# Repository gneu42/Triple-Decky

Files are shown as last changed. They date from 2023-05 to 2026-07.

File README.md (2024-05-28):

<h1 align="center"><ins>Triple-Decky Filament Block</ins></h1>

<H2 align="center">Filament block with  triple decks for ERCF V1/V1.1, Sturdy Bunny and ERCF V2.</H1>

## What is it ?

**Triple Decky** is based on the Sturdy Bunny filament block from **Sneakytreesnake** that incorporate the MR85ZZ bearing making the need for bearing blocks obsolete. It is a replacement for the filament block on ERCF V1 and Sturdy Bunny. Its goal is to avoid the filament to move in or out the filament block while loading or unloading another gate.
To do that, the filament block consist in 2 hinged parts (decks), that are kept apart by magnets. The filament is lifted by 1 mm from the bottom BMG gear.
The tophat comes on top of the 2nd deck and has the top BMG gear as before.
An integrated tophat based on number 1 tophat locker to be used with Springy [from Moggieuk](https://github.com/moggieuk/ERCF-Springy/tree/main) on Rev B and C.
Although Rev B version still has the possibility to install the magnetic gate, it is normally not needed anymore.
It will not be possible to install the magnetic gates on Rev C.
The width is 23.05mm as the latest Sturdy Bunny filament block that incorporate the bearing in the block.
To take all the benefit of the Trple Decky Filament Block, it is recommended to use a good buffer system (preferably a single loop buffer) The PTFE tube should not apply down force on the ECAS so the magnet can do their work correctly.
For people who needs a bypass block, there will be one incorporated in the "filament block end" of ERCF V2. A stand alone Bypass block that can be placed anywhere on the 2020 extrusion is also available on the triple decky Github. (Bypass_with_ECAS.STL) 
***
## Summary.
* **[Bom](#bom)**
* **[Printing Tips](#printing-tips)**
* **[Cleaning tips](#cleaning-tips)**
* **[Assembling tips](#assembling-tips)**
* **[Triple Decky for Sturdy Bunny and ERCF V2](#triple-decky-for-sturdy-bunny-build-on-a-2020-extrusion)**
  * **[Revision C for 3 positions servo "3PS"](#triple-decky-for-3-positions-servo-brake-release)**
    * **[Important note about Rev C 3 positions servo](#important-note-about-the-3ps-version)**
  * **[Revision C for magnet release brake ](#triple-decky-for-magnet-brake-release)**
  * **[Revision B ](#triple-decky-rev-b)**
* **[Triple Decky for ERCF 1.1](#triple-decky-for-ercf-v1)**
***
## Latest updates.

* #### Savox Servo arm C9 for original horn <sub>*May 28, 2024*</sub>
  * In my opinion, the weakest point of the ERCF are the servo splines. This servo arm solves that problem by using the original 4 branches horn delivered with the Savox servo. It will also work with trimmed MG90 horn. 
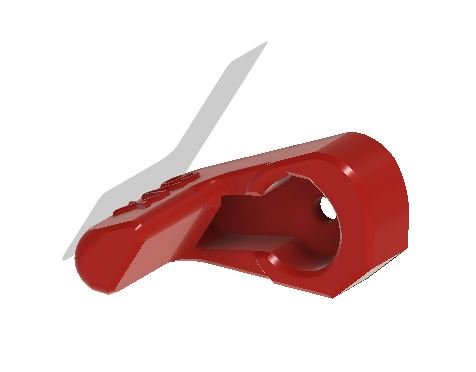
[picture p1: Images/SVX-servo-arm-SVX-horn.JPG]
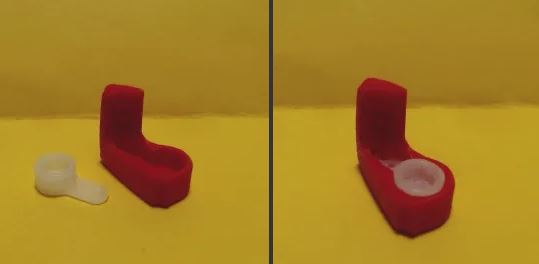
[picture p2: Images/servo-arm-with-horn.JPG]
servo-arm-with-horn
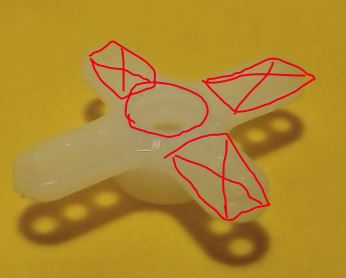
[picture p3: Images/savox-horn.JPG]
   
* #### Triple Decky C9.x <sub>*Apr 27, 2024*</sub>
**<p align=center>If this is your first time printing Triple Decky, it is best to print the C9.x version. However if you have already printed the C7.x parts, and they are freely working together, there is no benefit to upgrade to C9.<br> </p>**
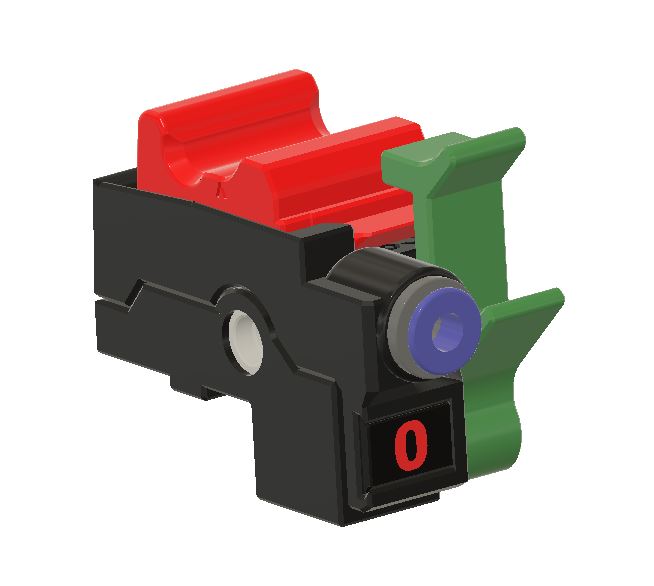
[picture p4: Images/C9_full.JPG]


  * Revision C9.x brings an almost build-in supports free. There is still one build-in support on the tophat.
    * The latch is modified for better integration with Cotton Tail and the new modified base. 
    * The base is shorter and the small latch centering part should not break anymore if the screw is screwed in correctly.
    * The entry tag plate is move from the base the filament path. This makes it easier to install the tag plates after the ERCF unit is build and functioning. The tag plates can then be printed in multi-color with the freshly build unit.
    * The trap design is modified to accommodate the support free base. It is now connected to the base with an M2x10 screw.
    * The tophat has a lower profile than the previous version. This should fix the servo down problem that some users have encountered.
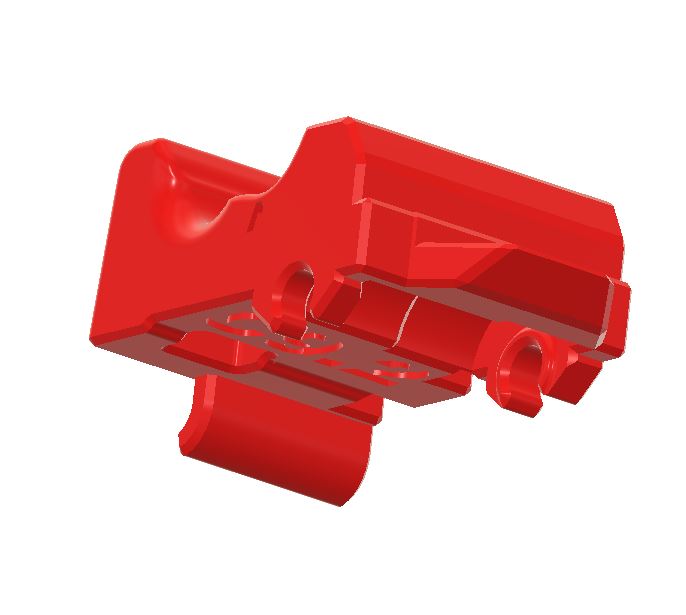
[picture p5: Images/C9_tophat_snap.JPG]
    * There is an optional tophat with sanp-in BMG.
    * There are 2 versions of C9S which incorporate a pre-gate sensor Those versions are made for people with limited space and that does not want to use the Cotton Tail version of the pre-gate sensors.
      * This version of pre-gate sensor is optimized to avoid false triggerinig if the filament have a notch ground from previous bad load.
      * The 5.5mm ball is replaced by a 6x3mm magnet for more stability of the anti-false triggering device.
      * Although this version works very well for automatic insertion of the filament, it may or may not work well for endless spool. 
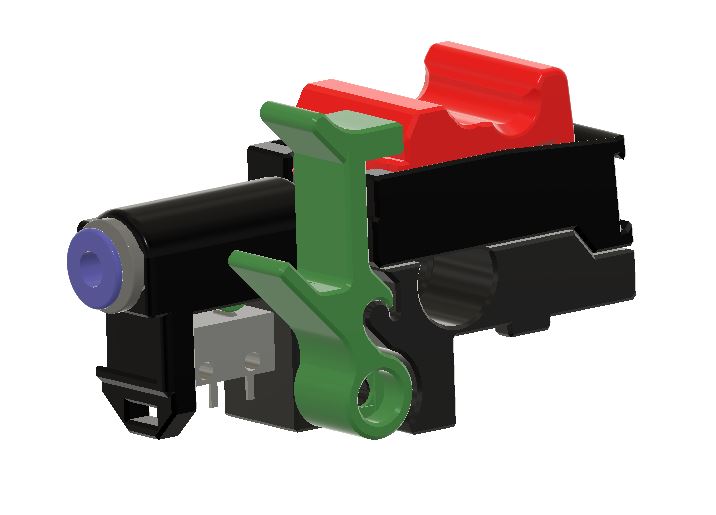
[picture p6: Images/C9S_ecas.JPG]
      * One version uses an ECAS to hold the PTFE tube.
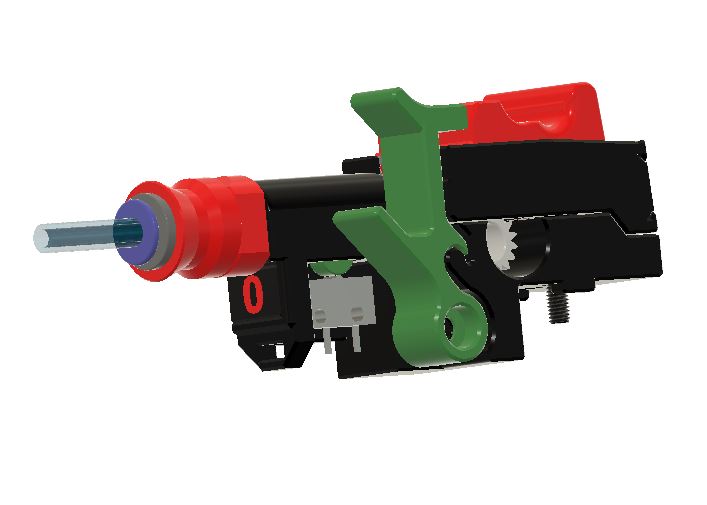
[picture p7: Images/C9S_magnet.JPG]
      * The other uses magnets to hold the PTFE in the filament path.

  * The C9S Pre-gates Sensor STL are in the **Optional Pre-gate Sensor** folder of Rev_C9. See readme file of the folder for more details.
  
  **IMPORTANT NOTE : The C9.x parts are not compatible with the previous C7.x version.**

* #### Triple Decky C7.0 <sub>*Oct 11, 2023*</sub>

  Revision C7.0 brings a few changes to the 3 main parts of Triple Decky. 
  * The big change is on the tophat that gives 2 alternatives. 
    * In one single part with a better support
    * In 2 parts with one support only. The 2 parts are screwed together with M2x10 self tapping screws.
    * This new revision applies only to the 3 positions servo. It will not be compatible with encoder that has the old magnets that were opening the gates on ERCF V1.1
  * The filament path has 2 main changes 
    * It width is reduced by 1 layer (0.2mm) to make sure that they do not rub against each other in case the blocks are installed too tight together.
    * The main support geometry is changed to be easier to print and removed.
    * Two optional clearance versions are available in the clearance option folder. This should make it easier to print with "not too well" tuned printers.
      * the female hinge of Clearance1 is 0.1mm wider than the default part.
      * the female hinge of Clearance2 is 0.2mm wider than the default part.
  * The base has no significant changes beside the 2 clearance options. Also available in the clearance options folder.
  * Tag plates are now available up to 15 gates.

  ##### Tophats C7.0   

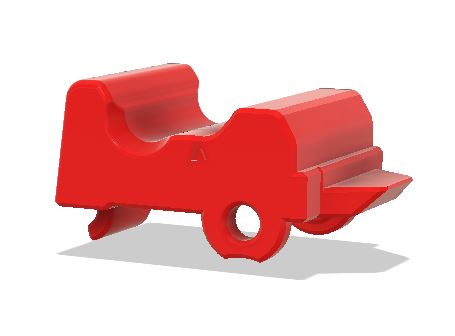
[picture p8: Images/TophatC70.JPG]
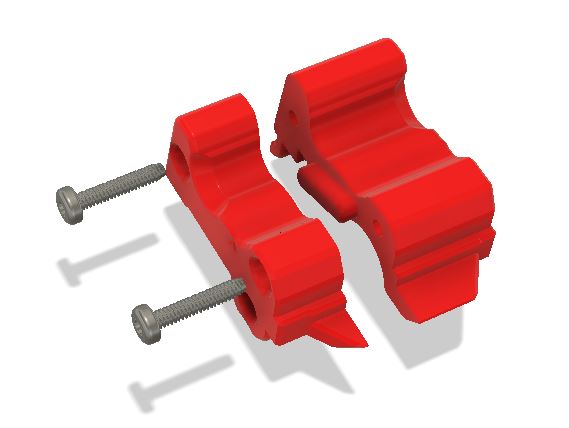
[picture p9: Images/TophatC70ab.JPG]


On the clearance option parts, there are 1 or 2 dots beside the code "C7.0" for the 0.1mm and 0.2mm wider cavities.

  ##### Filament Path C7.0
  
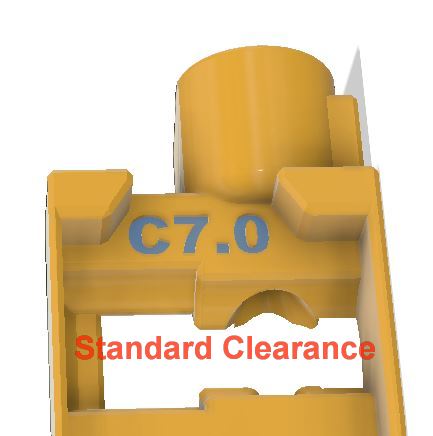
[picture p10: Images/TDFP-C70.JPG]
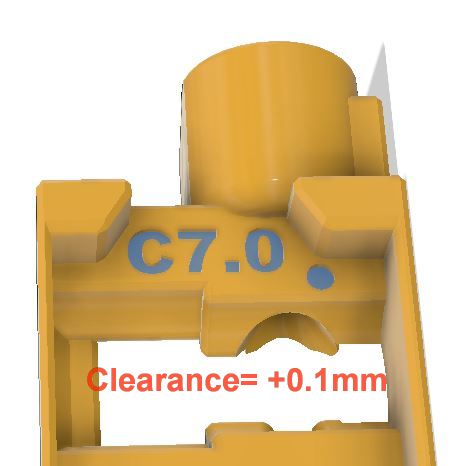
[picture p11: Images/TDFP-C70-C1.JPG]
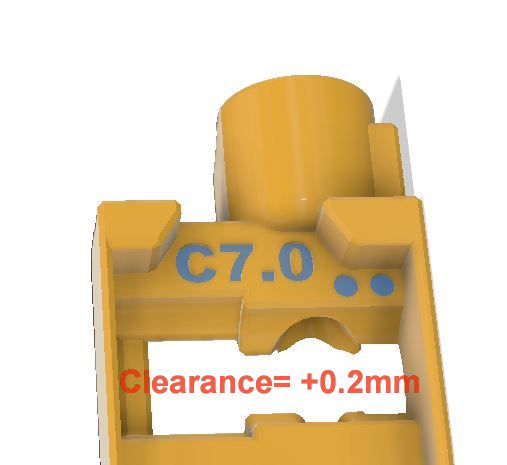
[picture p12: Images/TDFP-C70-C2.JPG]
<p align=center>  
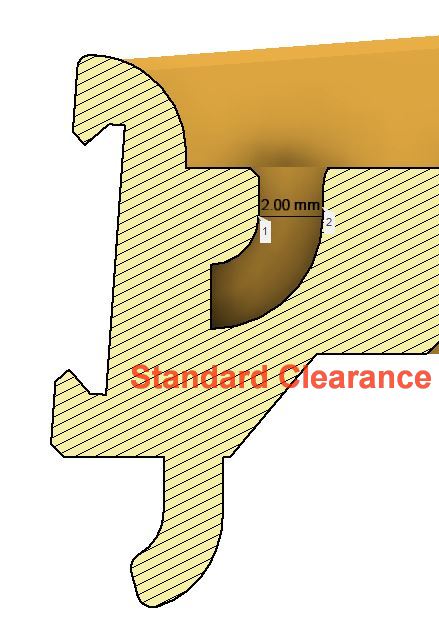
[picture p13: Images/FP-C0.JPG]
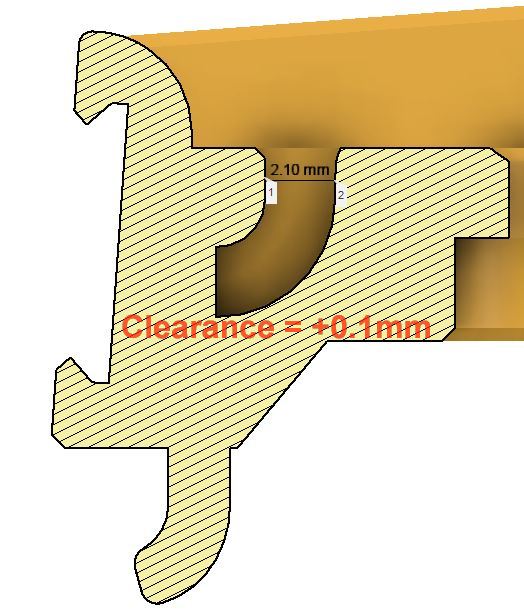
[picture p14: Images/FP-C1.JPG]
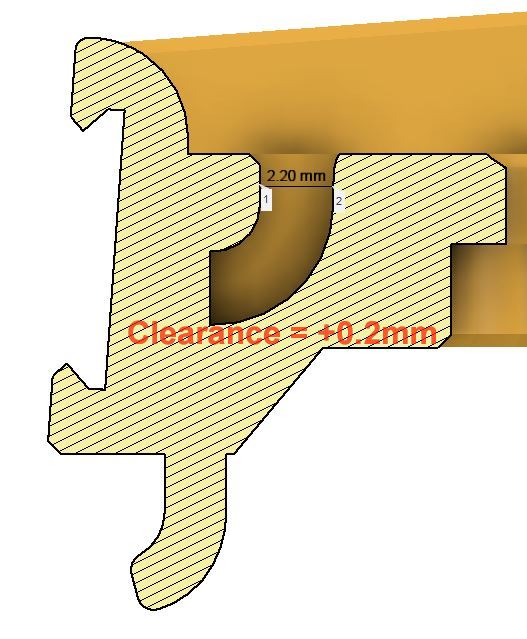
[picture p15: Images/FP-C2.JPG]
<p align=center>  

  ##### Base C7.0

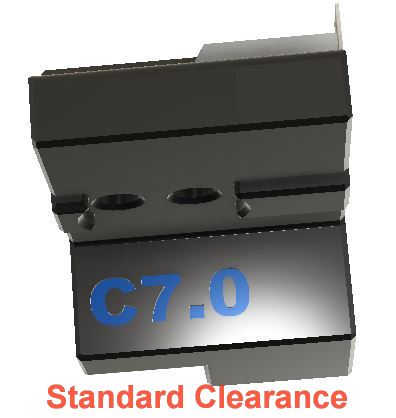
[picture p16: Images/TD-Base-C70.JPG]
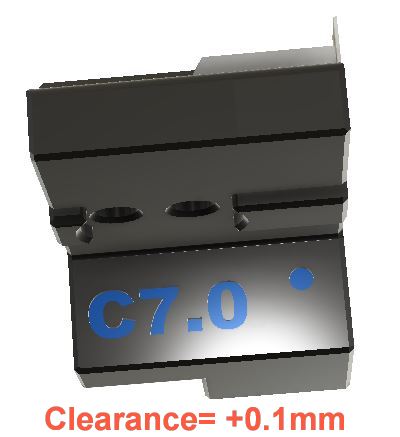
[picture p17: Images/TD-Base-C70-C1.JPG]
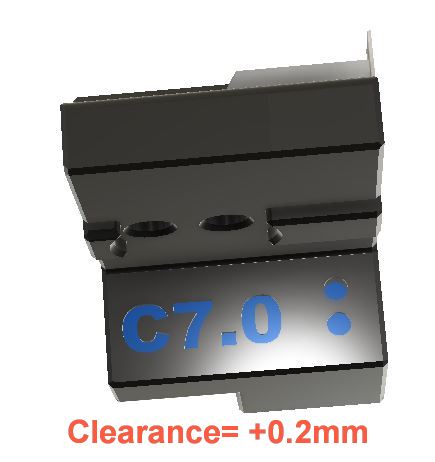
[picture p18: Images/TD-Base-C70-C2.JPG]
<p align=center>  

* #### Triple Decky Base C6.3. <sub>*Aug 31, 2023*</sub>
  
  No change in the main geometries. Only aesthetic change to blend better with filament path C6.3.

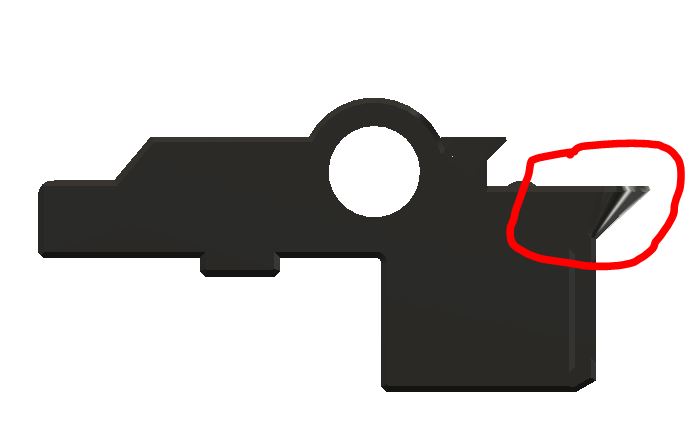
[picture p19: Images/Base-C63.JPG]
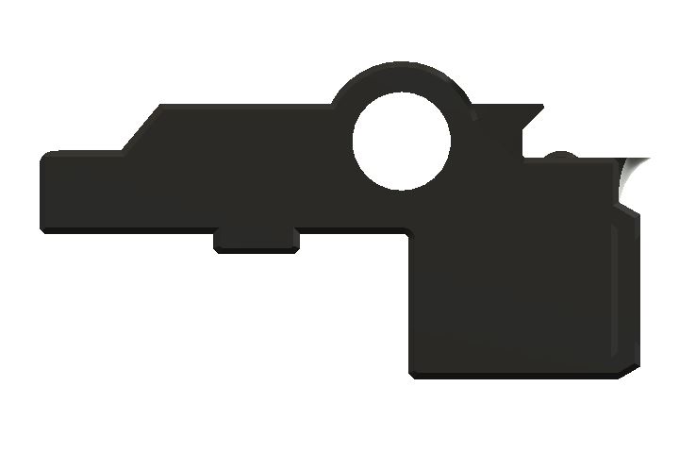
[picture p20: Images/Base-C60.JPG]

<p align=right><sub>You can still find the Triple_Decky_Base_C6_0.stl in the archive folder.</sub>

* #### Stand alone Bypass Block with ECAS. <sub>*Aug 25, 2023*</sub> 
     
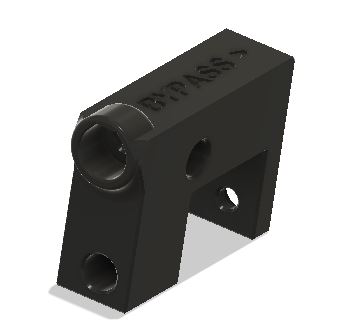
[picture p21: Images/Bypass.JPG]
   <p align=center>You can find it in stl/sturdy bunny</p>
  
* #### New Filament Path Rev C6_3. Read more about it [here](#update-6_3). <sub>*Aug 25, 2023*</sub> 

* #### Triple Decky Rev C for 3 positions servo STLs. Make sure to read the [Important Note Below](#important-note-about-the-3ps-version) first !!!

* #### Triple Decky Rev. C. Read the details [here](#triple-decky-rev-c)

***
## **Yet in development :**
* **ERCF V2 :** at this moment, ERCF V2 is in development by a team of designers. Lots of things have been developed and are tested, but regarding the filament blocks, no decision have been taken on which version of Triple Decky or another type will be used.
  * Mods in progress :
    * Sturdy Bunny: https://github.com/sneakytreesnake/SturdyBunnyProject
    * Springy: https://github.com/moggieuk/ERCF-Springy/tree/main
    * Ejection Assisted Purge: https://github.com/bombela/EjectionAssistedPurge
    * Binky: https://github.com/mneuhaus/EnragedRabbitProject/tree/main/usermods/Binky

**I have re-structured this GitHub to show only the latest versions of each type. All previous STLs are available in the Archives folder.**
***
## BOM.
For each block you need :  
  * #### Rev B.
    * 1 M3x8 SHSC (to mount the base on the 2020 extrusion)
    * 1 M3x16 SHSC (to mount the latch on the base)
    * 2 6x3 magnets (between the base and the filament path)
    * 1 ECAS (on the filament path)
    * 1 set of BMG (on the D-shaft in the base and in the top hat)
  * #### Rev C magnet release trap.
    * 1 M3x8 SHSC (to mount the base on the 2020 extrusion)
    * 1 M3x16 SHSC (to mount the latch on the base)
    * 1 M3x3 set screw. Length: from 2 to 3mm (to install in the trap) (M3x2 can be found in BMG).
    * 3 6x3 magnets (between the base and the filament path and at the back of the filament path)
    * 1 ECAS (on the filament path)
    * 1 set of BMG (on the D-shaft in the base and in the top hat)
  * #### Rev C 3 positions servo release trap.
    * 1 M3x8 SHSC (to mount the base on the 2020 extrusion)
    * 1 M3x16 SHSC (to mount the latch on the base)
    * 1 M3x3 set screw. Length: from 2 to 3mm (to install in the trap) (M3x2 can be found in BMG).
    * 2 6x3 magnets (between the base and the filament path)
    * 1 ECAS (on the filament path)
    * 1 set of BMG (on the D-shaft in the base and in the top hat)
    * Optional : 2 M2x10 self tapping screws for the 2 parts tophat.<p>
   
   <font size="2">[Summary](#summary)
*** 
## **Printing tips:**
  * Make sure your **printer is well tuned**, especially the first layer height. If it is too thick, the brake (trap) will be too thick and will not move freely inside the filament path.
  * All STL were tested OK with ABS and ABS+ 
  * Use voron standard print profile ( I use Andew Ellis ABS print profile).
  * **The hinged parts are the trickiest.** Make a test with one set of parts to see if they fit together freely. Some users have reported that decreasing the "extrusion multiplier" by a few %, makes the parts go together much better. 
  * The 3 main parts are fitting together using a kind of hinge. They should fit together without filing and with a little bit of play. 
  * For unknown reason, Super Slicer and Prusa slicer reports 6 open edges on the filament path STL. **DO NOT try to fix it**, otherwise you will have support that are filled up with infill and more than one perimeter thick. 
  * Make sure you have "Thin wall" enable, otherwise you won't have supports. Set also the speed for thin wall around 50% of the external perimeter speed.
  * It is also better to print a few spare traps. The sides are quiet thin, and it could be possible to break one if you remove the filament path too often.
  * If you plan to print the tag plates in multicolor :
    * You already have a working ERCF, then no problem, just print them before assembling ERCF V2
    * This is your first ERCF build. Then you have 2 possibilities.
      * You can print them multicolor the old way, by changing color manually. The change of color is only 4 layers high, so it is not so difficult.
      * You can print them after you have your new ERCF V2 working, and install them.
        * On the base, you will have to shift each of the bases to allow the insertion of the tag plate
        * On the Filament Path, just remove it, insert the tag plate and re-install the Filament Path. <p>
  
   <font size="2">[Summary](#summary)
***
## **Cleaning tips:**
  * All support should come off very easily.
  * There should be very little part cleaning necessary
    * Using a 2mm drill bit, clean the filament path
    * using a needle file, clean the rectangular hole where the trap is going in on the filament path
    * The trap part should have a thickness of 3.05mm, use a file to make it <= 3.05mm or tune your first layer.
    *  Make sure that the rectangular hole in the filament path Rev C is clean so the trap/brake can fit loosely in. There should be 0.5mm clearance.
    * On the screw trap part you need to make sure that there are no plastic between the thread of the set screw and the filament. Use a sharp x-acto knive to open the space between the 2 holes.
   
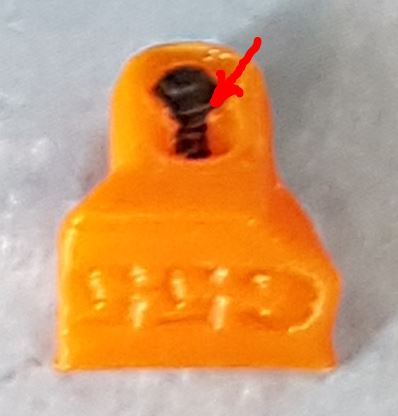
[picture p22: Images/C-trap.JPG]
    
    
    * On Rev C with magnet brake release, make sure the hole for the back magnet is clean, the magnet should go down against the bottom of the hole.  
    * On the tophat up to version C6.2 it could be possible that depending on the type of ABS(+) you're using, the tophat does not move as freely as needed. To solve that, you can cut or file down one layer off from the tang on the support side. This is fixed in the next version C6.3. I only encounter that problem with my ESUN Green ABS+.

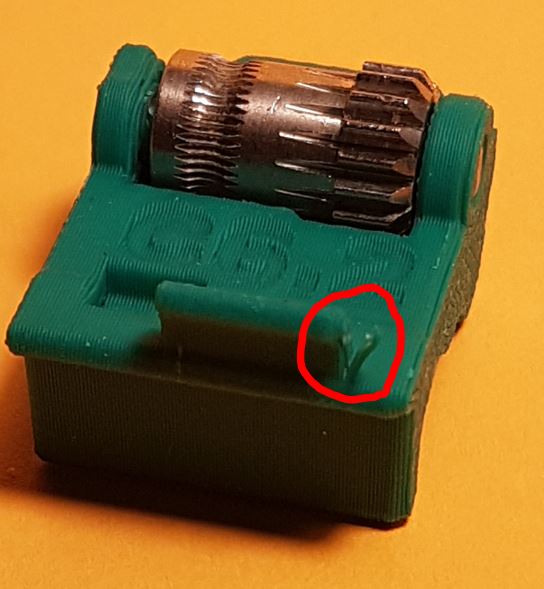
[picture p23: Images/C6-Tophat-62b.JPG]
    
      
       <font size="2">[Summary](#summary)
***
## **Assembling tips:**
**For all Triple Decky versions, when installing the blocks on the 2020 extrusion, it is not necessary to press the blocks firmly together. Just install them on the 2020 extrusion next to each other and tighten the screw. If you press them too much together, it is possible the filament pass does not move freely between their neighbors. This problem is solved in Revision C7.0**
  * Rev B is self explanatory. The 3 parts goes together by sliding the tangs into the correponding cavities that makes the hinges.
  * Rev C need a bit more attention to assemble the filament path on the base.
    * 1. Insert the M3x8 SHCS screw into the side hole of the base before installing the filament path. You will be able to access the screw through the filament pass later. (If you want to use 4 magnets, than you need to install the base on the 2020 extrusion before installing the magnets and filament path. 4 magnets are normally not necessary.)

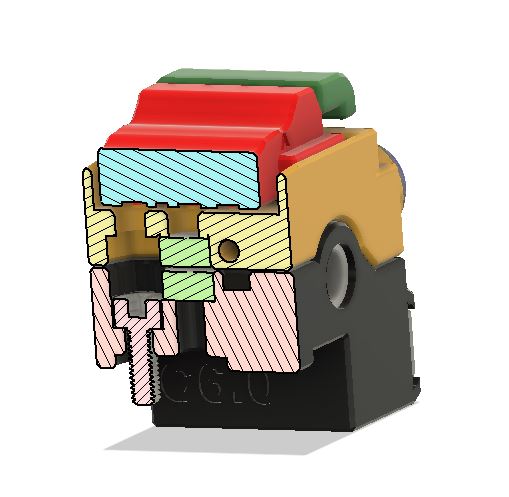
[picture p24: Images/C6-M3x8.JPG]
      

    * 2. Insert the magnet into the middle holes of the base and the filament path. The magnet must repell each other.
      * Optionally, you can use another set of magnet into the side holes if needed. In that case, the screw will be unaccessible without disassembling the parts
    * 3. Insert the trap into the female dovetail.
      * If you use the screw trap, insert the set screw at a slight angle. The 2 holes are angled by about 2°. Insert the set screw in the top hole. <BR>
      The set screw can be :
        * M3x3mm
        * M3x2.5mm
        * M3x2mm, the same that you can find in the BMG.   
       
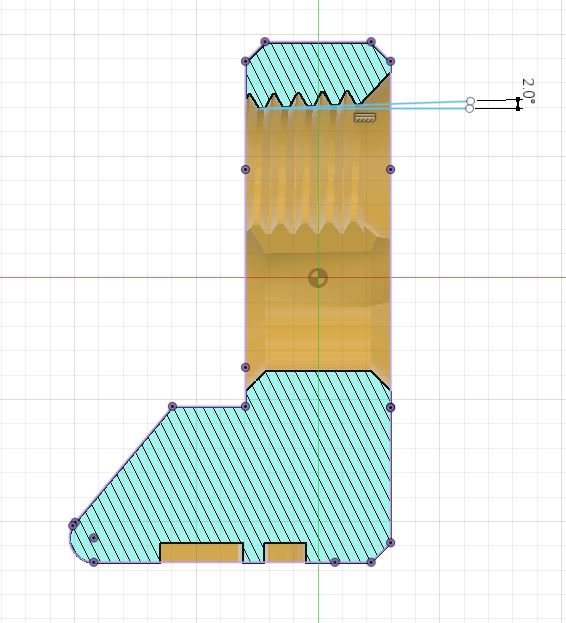
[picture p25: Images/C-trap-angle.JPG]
      

    * 4. Align the filament path above the base so they are parrallel and the top of the brake (trap) is "almost" inside his corresponding hole in the filament path and the tang of the hinge is just above the cavity of the base. 
     
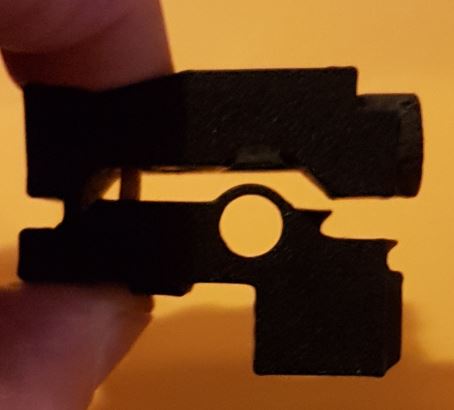
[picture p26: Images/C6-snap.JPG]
      
    
    * 5. Press firmly the filament path into the base. It snap into place easily.
    
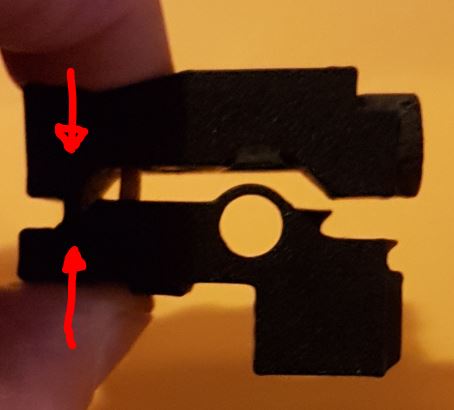
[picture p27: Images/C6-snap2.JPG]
      

  * Magnets orientation.
  
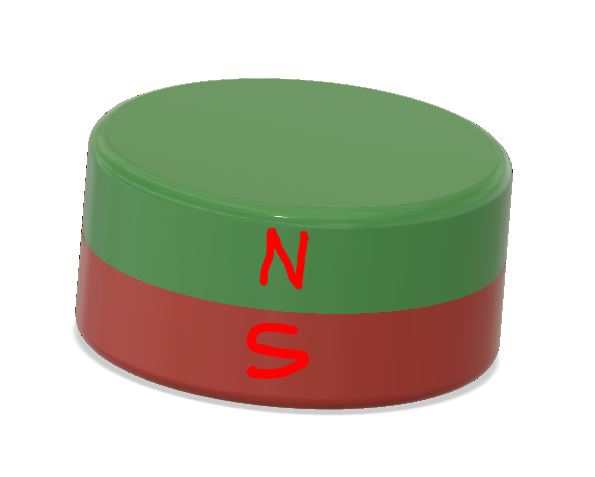
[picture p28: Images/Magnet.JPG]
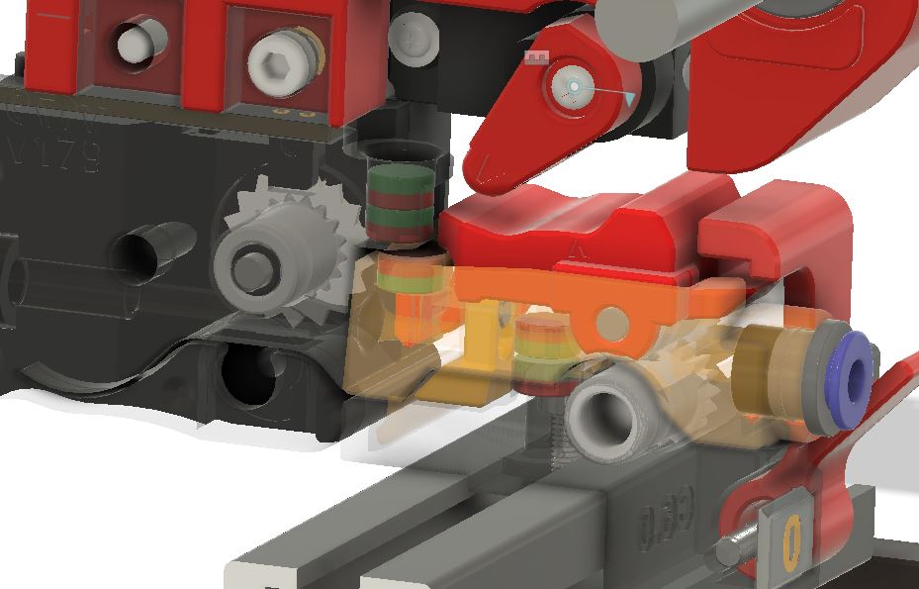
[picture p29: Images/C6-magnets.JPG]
       

  * Assembling video.<br>
  This video shows how parts fits together out of the printer without any filing nor sanding. Then how Triple Decky works with one pair of magnets and the movement you should have at the back and front side. And finally how to install the trap.
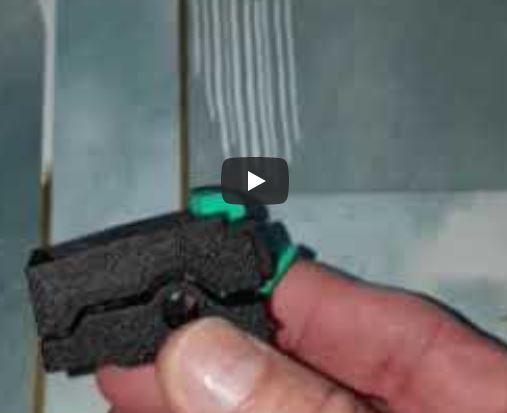
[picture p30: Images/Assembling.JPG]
Assembling
   <p align=center>  

<font size="2">[Summary](#summary)

***
## Triple Decky for Sturdy Bunny build on a 2020 extrusion 
 ### Triple Decky Rev C
   **It is an evolution of Rev B. with the following new features.**
   *  It has a kind of brake to press against the filament when the gate is not selected. The exit side of the filament path can lift up about 0.5 mm, enough to make the filament touching the brake part (trap). To release the brake it will use either :
        *  with a magnet that will be pushed back by the encoder magnet.
        *  by using a special tophat that will need a 3rd position of the servo to be able to move the selector. (software in development)<p>
   * The brake part will be easily replaceable in case it breaks.
   *  The multi-color tag plates will be the same for input and output side. (Same as in version B4 Base)<p>
   *  The use of the old magnetic gates will be **impossible** on that version.
   *  If you are using Happy Hare software, you should decrease the "parking_distance" in the ercf_parameters to about 15 so the filament parks inside the trap.
   *  It is normal that the filament does not pass the trap when inserted manually. When the gate will be selected, Happy Hare will load it without problem. If you want to lock it inside the trap, than you need to push down the exit side of the filament path with your finger and insert the filament about 5 mm further.<p>

<font size="2">[Summary](#summary)
***  
### **Triple Decky Rev C6 magnet brake release or 3 positions servo.** 

#### Update 6_3 
 This update concern all **Filament Path revision B and C for Sturdy Bunny**. The ECAS is moved 4mm out to enable the insertion of the PTFE tube inside the part. I recommend to use it over the previous versions.
 * This allow for easy threading of the filament and keeps also the geometry for Endless Spool function.
 * It avoids the ECAS to go slowly out of its cavity after some time.

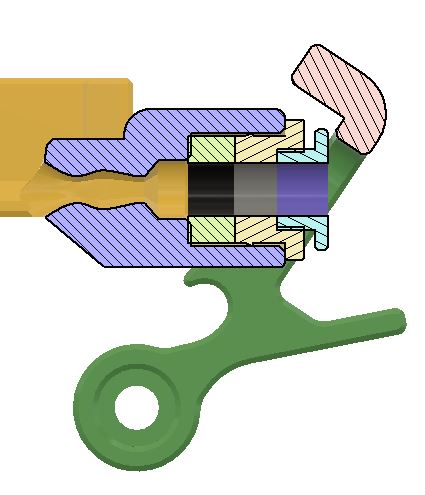
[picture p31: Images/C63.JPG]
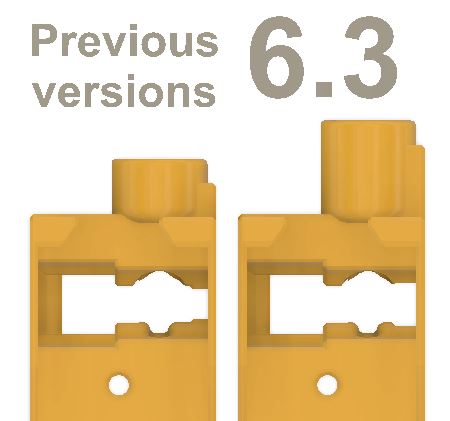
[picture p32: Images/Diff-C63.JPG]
      

#### Update C6 
This is an update from Rev C5 that fixes the following issues:
  * wall around the bearing cracks
  * filament path output side rubbing on the encoder and get pushed down. 
  * **It has the following new feature :**
    * thicker wall around the bearing
    * output face of the filament path is tilted 4° to avoid rubbing on the encoder cart
    * new tophat to match the brake release magnet new position

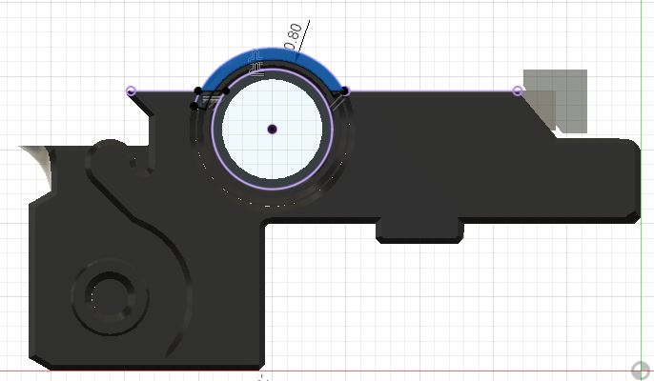
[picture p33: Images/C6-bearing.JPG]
C6 bearing
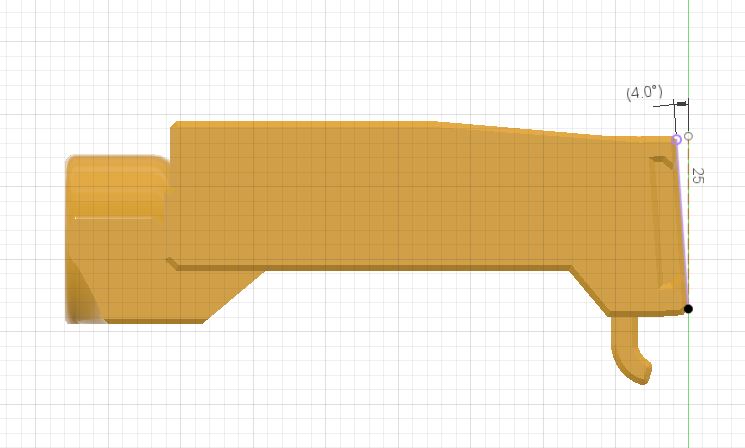
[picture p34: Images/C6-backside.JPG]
        

  * **Warning:**
          * C6_x base need to have C6_x filament path
          * C6_x filament path need to have C6_x tophat
          * C5_x base is compatible with C6_x filament path
          * C5_x filament path is compatible with C6_x tophat
          * For all Rev C, only the integrated tophat are available, and needs the Springy servo holder to work. (see above in mods in progress) <p>
      <p>
           
***
### **Triple Decky for 3 positions servo brake release**

   * This version uses the servo to push the filament path down so the filament is free to move when the gate is selected.
   * When the gate is not selected, the filament will be hold still by the trap.
   *  New integrated tophat based on number 1 tophat locker to be used with Springy [from Moggieuk](https://github.com/moggieuk/ERCF-Springy/tree/main) 
    
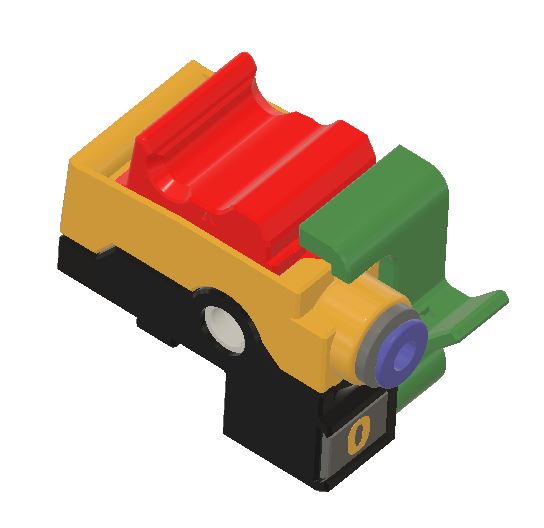
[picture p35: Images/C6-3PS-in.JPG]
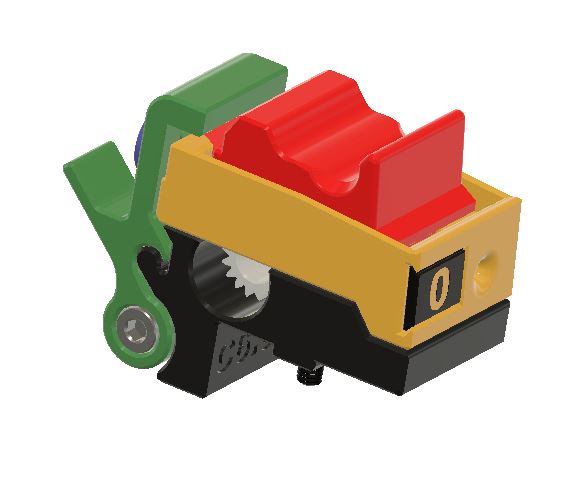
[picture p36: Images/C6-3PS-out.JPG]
      <p>
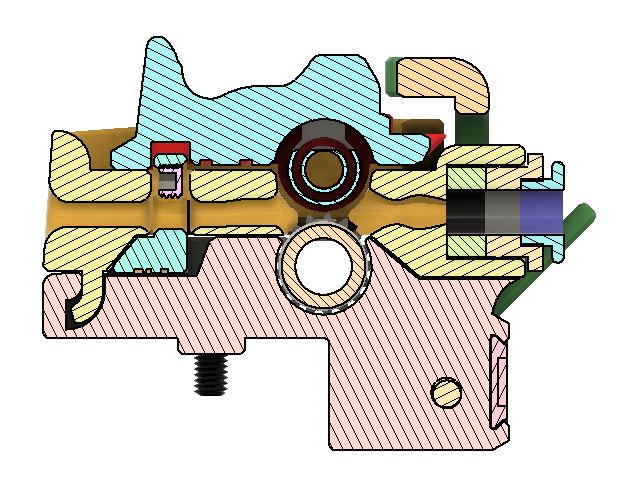
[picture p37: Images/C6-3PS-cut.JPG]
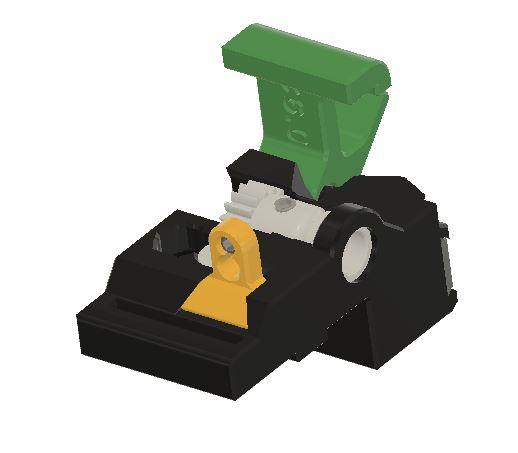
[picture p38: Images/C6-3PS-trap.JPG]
C5 trap
      
  
  <font size="2">[Summary](#summary)

#  **IMPORTANT NOTE ABOUT THE 3PS VERSION.**
   *  **If you want to use the C6 with 3 positions servo YOU HAVE TO USE the latest Happy-Hare software (HHv2) that support the servo 3rd position. It is public now. Otherwise IT WILL NOT WORK.   <br> You need also to update KlipperScreen for Happy Hare.**
   * The base is the same for both Rev C versions (Triple_Decky_Base_C6_3.stl).
   * The taps are the same for both Rev C versions (Traps folder).
   * If you are already using the magnet version, you can still use it if you print the universal tophat ([a]Triple_Decky_Tophat-integrated_Universal_Mag&3PS_C6_3.stl). **DO NOT USE THIS STL IF YOU DO NOT HAVE ENABLED THE 3rd POSITIONS FOR SERVO IN YOUR SOFTWARE!!!** <br> **You must have the servo_move_angle defined in the mmu_parameters.cfg**
   * If this is your first use of Rev C 3PS, then it is better to use the dedicated tophat for 3PS ([a]Triple_Decky_Tophat-integrated_3PS_C6_3.stl).
   * For better results, you should use the special servo arm with rounded edges for this repo (Servo Arm MG90S_for_3PS.stl or Servo_Arm_Savox_for_3PS.stl) .
   * **Software parameters** 
     * Add "servo_move_angle: (move position angle)" in mmu_parameters.cfg
       * **For MG90S**
           * servo_move_angle: 45
           * servo_up_angle: 24
           * servo_down_angle: 115
          <p>
       * **For Savox SH0255MG**
           * servo_move_angle: 95
           * servo_up_angle: 115
           * servo_down_angle: 45
         
      * Change the "encoder_parking_distance:" in mmu_parameters.cfg so the filament parks in the trap. (for me I change it to 15, it was 23) 
  
   * **Servo positions**<br>
      Make sure to adjust the 3 position of your servo arm so the arn does not hit the tophats when the selector is moving. See picture below to fiind out where the position should be for the 3 positions.
  
       * Servo Up. (trap released / print without sync)
  
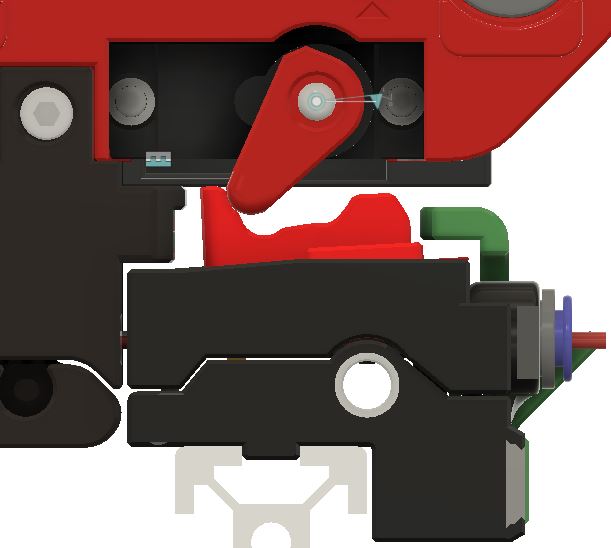
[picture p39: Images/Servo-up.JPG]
       

       * Servo Move. (trap locked / selector movement)

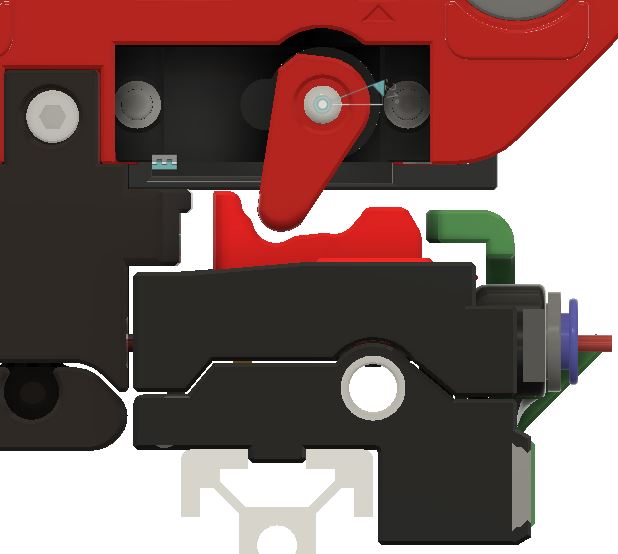
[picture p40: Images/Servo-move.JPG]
       

       *  Servo Down. (trap released for Load/unload or print with sync mode)
  
             <p>
 
  * **Servo arm geometry for 3 positions servo** <br>
      The servo arm is based on the Springy servo arm. To have a better effect when using the 3 positions servo, the geometry is modified as shown on the picture below. The blue area shows the added part. This make the "UP" position pushing a bit more to release the trap. The length is also increased by about 0.3mm in the "DOWN" position. It is, therefore, better to use it with Springy from [@moggieuk](https://github.com/moggieuk/ERCF-Springy/tree/main).
      This version is available for MG90S and Sävox SH-0255-MG in the "Rev_C/Filament_Path_for_3_position_Servo" sub-directory of this repo. 

. 


  * **Servo splines differences** 
      The servo arm splines are different between the MG90S (blue shade on the picture) and the Sävox SH-0255-MG (in red on the picture). Be sure to use the arm the matches your servo.



<font size="2">[Summary](#summary)
***
### **Triple Decky for magnet brake release**

   * This version uses the encoder magnet to push the filament path down so the filament is free to move when the gate is selected.
   * When the gate is not selected, the filament will be hold still by the trap.
  *  New integrated tophat based on number 1 tophat locker to be used with Springy [from Moggieuk](https://github.com/moggieuk/ERCF-Springy/tree/main)

       <p align=center>C5 in C5 out</p><p>
       <p align=center>C5 cutout C5 trap</p>

<font size="2">[Summary](#summary)
***
### **Triple Decky Rev B**

   * The output side of the filament path has been tilted by 4° to avoid rubbing on the encoder when the selector is moving.
   * The input side tag plate is rotated 90° for better printing without support.
   * New multicolor tag plates for 12 carts on the input side.
   * New multicolor gate plates for 12 carts on the output side to replace the magnetic gate. 
   * New integrated tophat based on number 1 tophat locker to be used with Springy [from Moggieuk](https://github.com/moggieuk/ERCF-Springy/tree/main)  
   * optional base to use the old magnetic gates. In that case, the small part of the hinge of the filament path must be cut at the mark.
   * The latch has an optional set screw to apply a little bit of friction on the filament. This help the filament to stay still in case of vibrations.<p>
   * Since this version has no real brake system. It is better to use a single loop buffer system that provide more stability of the filament when it is in the buffer.
  
      
       
       <font size="2">[Summary](#summary)    
*** 
## **Triple Decky for ERCF V1**

   * This is for the original design that is build with M5 all threaded rod. This version will not be developed further because almost all users / builders are moving to Sturdy Bunny, or the coming (soon) ERCF V2.<p>
   
      <p align=center>Triple Decky for ERCF V1</p>

<font size="2">[Summary](#summary)

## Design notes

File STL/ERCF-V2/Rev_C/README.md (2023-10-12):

# **Some notes on how to use the version C6 and C7**
## **Warning**
* **Version  C6 and C7 only works with Sturdy Bunny or coming soon V2.**
* **Version C7 only works with Happy Hare V2 and his 3 positions servo capability.**
* **Version C7 tophat can't work if you have the 2 magnets on your encoder cart.**

* **For best results with the C6 magnet release trap, be sure to use **N52 Magnets** on the encoder and the top of the filament exit. Secure the magnets in the encoder with a drop of glue, otherwise they will pop out when they are above the gate magnet.**

 For all versions, print print the latch **[a]Triple_Decky_Latch_RevC6_0.stl** from the folder STL\Sturdy Bunny\Rev_C

## **What to print for Revision C7 for 3 positions servo brake release ONLY ?**
From folder ..\STL\Sturdy Bunny\Rev_C\Rev_C7.0_3PS_only
  * print either the **Triple_Decky_Base_C7_0.stl** and the **Triple_Decky_Filament_Path_3PS_C7_0.stl** 
    * If you experience problems with the parts not fitting freely together, you can try one of the extended clearance options under the **..\STL\Sturdy Bunny\Rev_C\Rev_C7.0_3PS_only\Clearance_options folder.**
  * print either the tophat : **[a]Triple_Decky_Tophat-Integrated_3PS_C7_0.stl**.
    * or the optional 2 parts tophat from the ..\STL\Sturdy Bunny\Rev_C\Rev_C7.0_3PS_only\2 parts tophat option folder **[a]Triple_Decky_Half_Tophat-integerated_3PS_C70a.stl** and **[a]Triple_Decky_Half_Tophat-integerated_3PS_C70b.stl**
  
From folder ..\STL\Sturdy Bunny\Rev_C\Tag_plates

  * print the multicolor **Triple_Decky_Tag_Plates_X.stl** from the **Tag_Plates** folder for the Triple_Decky_Base

From folder ..\STL\Sturdy Bunny\Rev_C\Traps 
  * print the trap of your choice from the Traps folder. Experiment to find the one that gives the better holding capability.
     *  **TD_Base_Trap_C5_Screw.stl** (This one needs a set screw M3x3)
      *  **TD_Base_Trap_C5_V-Shape.stl**<p>

From folder ..\STL\Sturdy Bunny\Rev_C\Servo_arms_for_3PS
  * print the servo arm corresponding to your servo.

## **What to print for Revision C6 for magnet brakes release ?**
From folder ..\STL\Sturdy Bunny\Rev_C\Rev_C6.3
  * print the **Triple_Decky_Base_C6_3.stl** 
  
From folder ..\STL\Sturdy Bunny\Rev_C\Rev_C6.3\Filament_Path_With_Magnets

  * print **Triple_Decky_Filament_Path_For_Magnet_C6_3.stl** 
  * print the tophat : **[a]Triple_Decky_Tophat-Integrated_For_Magnet_C6_3.stl**.

From folder ..\STL\Sturdy Bunny\Rev_C\Tag_plates

  * print the multicolor **Triple_Decky_Tag_Plates_X.stl** from the **Tag_Plates** folder for the Triple_Decky_Base

From folder ..\STL\Sturdy Bunny\Rev_C\Traps 
  * print the trap of your choice from the Traps folder. Experiment to find the one that gives the better holding capability.
     *  **TD_Base_Trap_C5_Screw.stl** (This one needs a set screw M3x3)
      *  **TD_Base_Trap_C5_V-Shape.stl**<p>

## **What to print for Revision C6 for 3 positions servo brake gates release ?**
From folder ..\STL\Sturdy Bunny\Rev_C\Rev_C6.3
  * print the **Triple_Decky_Base_C6_3.stl** 
  
From folder ..\STL\Sturdy Bunny\Rev_C\Rev_C6.3\Filament_Path_for_3_position_Servo

  * print **Triple_Decky_Filament_Path_3PS_C6_3.stl** 
  * print the tophat : **[a]Triple_Decky_Tophat-Integrated_3PS_C6_3.stl**.

From folder ..\STL\Sturdy Bunny\Rev_C\Tag_plates

  * print the multicolor **Triple_Decky_Tag_Plates_X.stl** from the **Tag_Plates** folder for the Triple_Decky_Base

From folder ..\STL\Sturdy Bunny\Rev_C\Traps 
  * print the trap of your choice from the Traps folder. Experiment to find the one that gives the better holding capability.
     *  **TD_Base_Trap_C5_Screw.stl** (This one needs a set screw M3x3)
      *  **TD_Base_Trap_C5_V-Shape.stl**<p>

From folder ..\STL\Sturdy Bunny\Rev_C\Servo_arms_for_3PS
  * print the servo arm corresponding to your servo.

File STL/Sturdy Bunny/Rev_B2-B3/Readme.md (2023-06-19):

# Important note about Filament Path

## **Some people have experienced the Filament_Path cracking when inserting the ECAS. To avoid that version B3.3 has a ECAS hole size 0.15mm wider than the original size. All other version prior and after B3.3 have all the original size.** 

## **If your printer is perfectly dialed in, DO NOT USE version B3.3, use B3.2 instead or the new B4.1 in Rev_B4 directory**

Only the print orientation of the ECAS hole is different from Sturdy Bunny. It is turn 90° for better printing and match with the original orientation of V1.1 from Ette.

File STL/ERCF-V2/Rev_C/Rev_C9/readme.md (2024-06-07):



  * Revision C9.x brings an almost built-in supports free. There is still one built-in support on the tophat.
    * The latch is modified for better integration with Cotton Tail and the new modified base. 
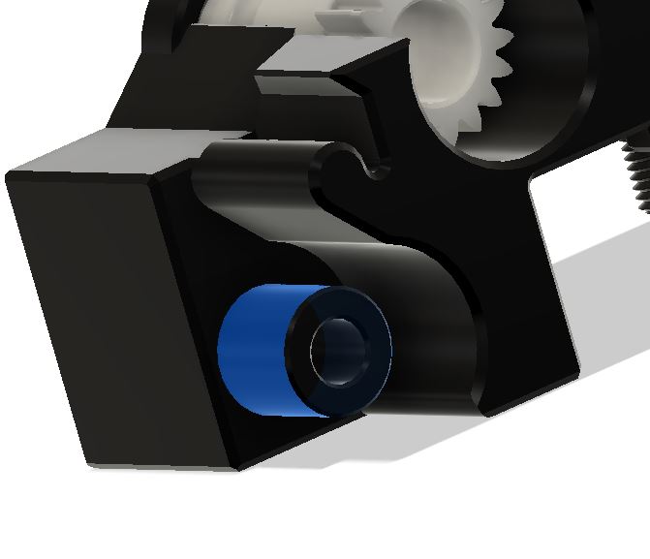
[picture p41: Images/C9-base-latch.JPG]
    * The base is shorter and the small latch centering part should not break anymore if the screw is screwed in correctly.
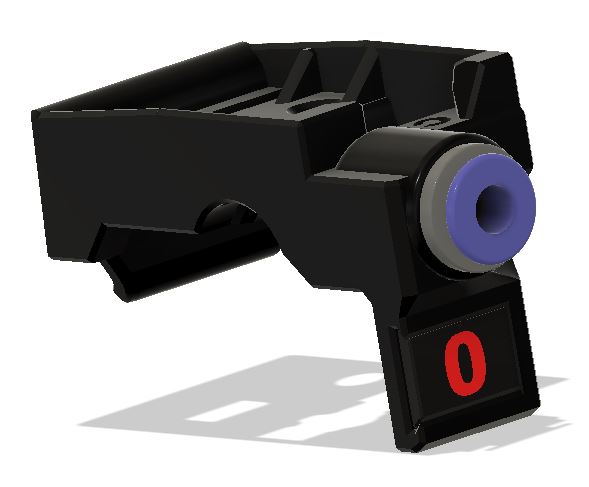
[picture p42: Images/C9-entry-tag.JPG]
    * The entry tag plate is move from the base to the filament path. This makes it easier to install the tag plates after the ERCF unit is build and functioning. The tag plates can then be printed in multi-color with the freshly build unit. Both tags are the same as C7.
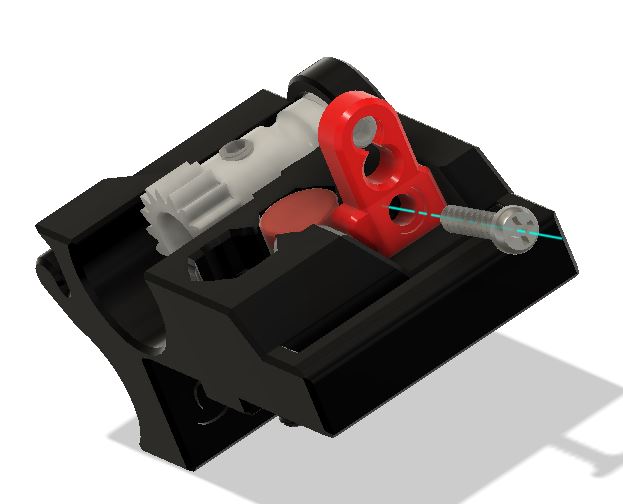
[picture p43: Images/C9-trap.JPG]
    * The trap design is modified to accommodate the support free base. It is now connected to the base with an M2x10 screw.
    * The tophat has a lower profile than the previous version. This should fix the servo down problem that some users have encountered.
    * There is an optional tophat with snap-in BMG.
    * **EXPERIMENTAL**. There are 2 optional versions of C9 called C9S which incorporate a pre-gate sensor Those versions are made for people with limited space and that does not want to use the Cotton Tail full or pre-gate version.
      * These versions of pre-gate sensor is optimized to avoid false triggering if the filament have a notch ground from previous bad load.
      * The 5.5mm ball is replaced by a 6x3mm magnet for more stability of the anti-false triggering device.
      * Although this version works very well for automatic insertion of the filament supported by Happy Hare, **it may or may not work well for endless spool**. 
      * One version uses an ECAS to hold the PTFE tube.
      * The other uses magnets to hold the PTFE in the filament path.

  * The C9S Pre-gates Sensor STL are in the **Optional Pre-gate Sensor** folder of Rev_C9. See readme file of the folder for more details.
  
  **IMPORTANT NOTE : The C9.x parts are not compatible with the previous C7.x version.**

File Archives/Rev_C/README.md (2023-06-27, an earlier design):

# **Some notes on how to use the version C5 and C6**
## **Warning**
Version  C5 and C6 only works with Sturdy Bunny or coming soon V2.
<p>
At this moment, the only version available is the trap release by magnet. When the software will be available, the 3 positions servo will be released.
<p>

## <center>For best results, be sure to use **N52 Magnets** on the encoder and the top of the filament exit. Secure the magnets in the encoder with a drop of glue, otherwise they will pop out when they are above the gate magnet.</center>

## **What to print for Revision C5 ?**

  * print the **Triple_Decky_Base_C5_3.stl** 
  * print **Triple_Decky_Filament_Path_With_Magnet_C5_3.stl** from the folder Filament_Path_with_magnets.
  * print the multicolor **Triple_Decky_Tag_Plates_X.stl** from the **Base_Tag_Plates** folder for the Triple_Decky_Base
  * print the tophat : **[a]Triple_Decky_Tophat_Integrated_For_Magnet_C5_3.stl**.
  * print the latch **[a]Triple_Decky_Latch_Beta3_1.stl**
  * print the trap of your choice from the Trap_Style folder. Experiment to find the one that gives the better holding capability.
    *  **TD_Base_Trap_C5_Round.stl**
    *  **TD_Base_Trap_C5_Screw.stl** (This one needs a set screw M3x3)
    *  **TD_Base_Trap_C5_V-Shape.stl**<p>

## **What to print for Revision C6 ?**

  * print the **Triple_Decky_Base_C6_0.stl** 
  * print **Triple_Decky_Filament_Path_For_Magnet_C6_2.stl** from the folder Filament_Path_with_magnets.
  * print the multicolor **Triple_Decky_Tag_Plates_X.stl** from the **Base_Tag_Plates** folder for the Triple_Decky_Base
  * print the tophat : **[a]Triple_Decky_Tophat-Integrated_For_Magnet_C6_2.stl**.
  * print the latch **[a]Triple_Decky_Latch_Beta3_1.stl**
  * print the trap of your choice from the Trap_Style folder. Experiment to find the one that gives the better holding capability.
    *  **TD_Base_Trap_C5_Round.stl**
    *  **TD_Base_Trap_C5_Screw.stl** (This one needs a set screw M3x3)
    *  **TD_Base_Trap_C5_V-Shape.stl**<p>

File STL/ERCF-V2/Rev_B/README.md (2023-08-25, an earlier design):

# **Some notes on how to use the version B4**
## **Warning**
 **Be really careful when inserting the Gate plates or the magnetic gates in the filament path. The way it is printed can cause cracks when inserting. Be sure the cavity is clean before inserting the gate plates.**

## **What to print ?**

 * **You want to use the new design without magnetic gates.**
   * print the **Trpile_Decky_Base_RevB4_1.stl** 
   * print **Triple_Decky_Filament_path_RevB6_3.stl**.   
   * print the multicolor **Triple_Decky_Tag_Plates_X.stl** from the **Base_Tag_Plates** folder for the Triple_Decky_Base.
   * print the **Tag_Gate_X.stl** from the folder **Filament_path_Tag_Gates** for the Filament path output side.
    * print one of the tophat :
      * **[a]Triple_Decky_RevB4_1_Tophat_integerated.stl** if you are using Springy. It may also work with original selector. It is based on number 1 Tophat locker
      * **[a]Triple_Decky_RevB4_1_Tophat.stl** if you want to use your original tophat lockers.
    * print the latch **[a]Triple_Decky_Latch_Beta3_1.stl**<p>

* **You want to use the old magnetic gates.**
  * print the **Trpile_Decky_Base_RevB4_1_Magnet.stl** from the folder **Optional for old magnetic gates**.
  * print **Triple_Decky_Filament_path_RevB6_3.stl** and cut the small part of the hinge. 
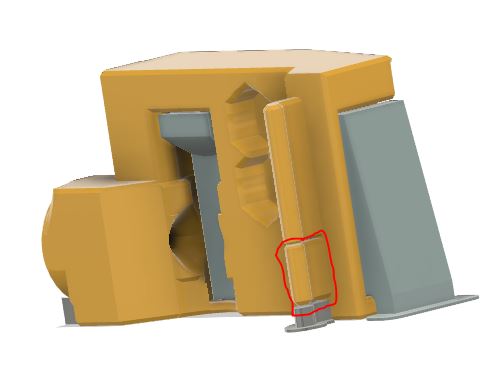
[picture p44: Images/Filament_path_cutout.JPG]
Hinge cut
    <p><p>
  * use your original magnetic gates.
  * print the multicolor **Triple_Decky_Tag_Plates_X.stl** from the **Base_Tag_Plates** folder for the Triple_Decky_Base
  * print one of the tophat :
    * **[a]Triple_Decky_RevB4_1_Tophat_integerated.stl** if you are using Springy. It may also work with original selector. It is based on number 1 Tophat locker
    * **[a]Triple_Decky_RevB4_1_Tophat.stl** if you want to use your original tophat lockers.
  * print the latch **[a]Triple_Decky_Latch_Beta3_1.stl** <p>

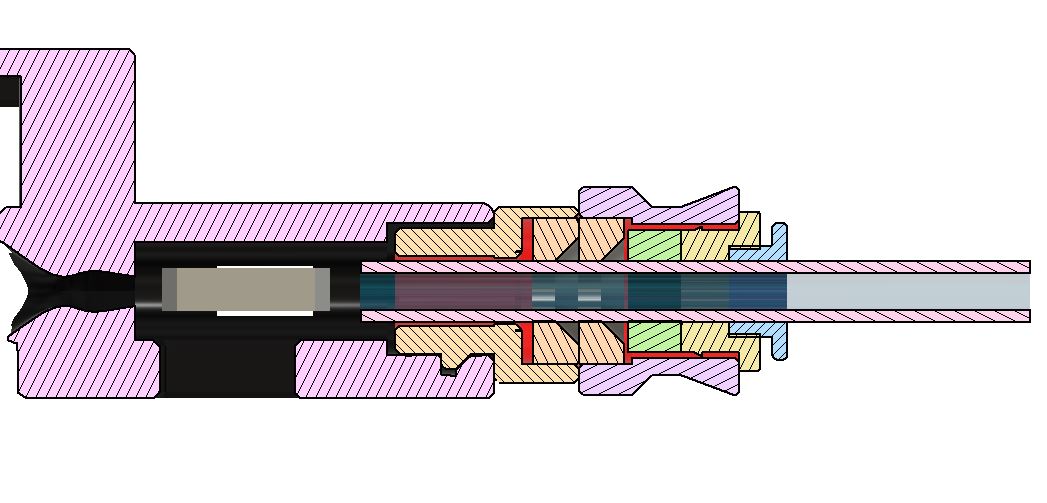
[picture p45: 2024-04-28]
Images/C9S_magnet_cutout.JPG

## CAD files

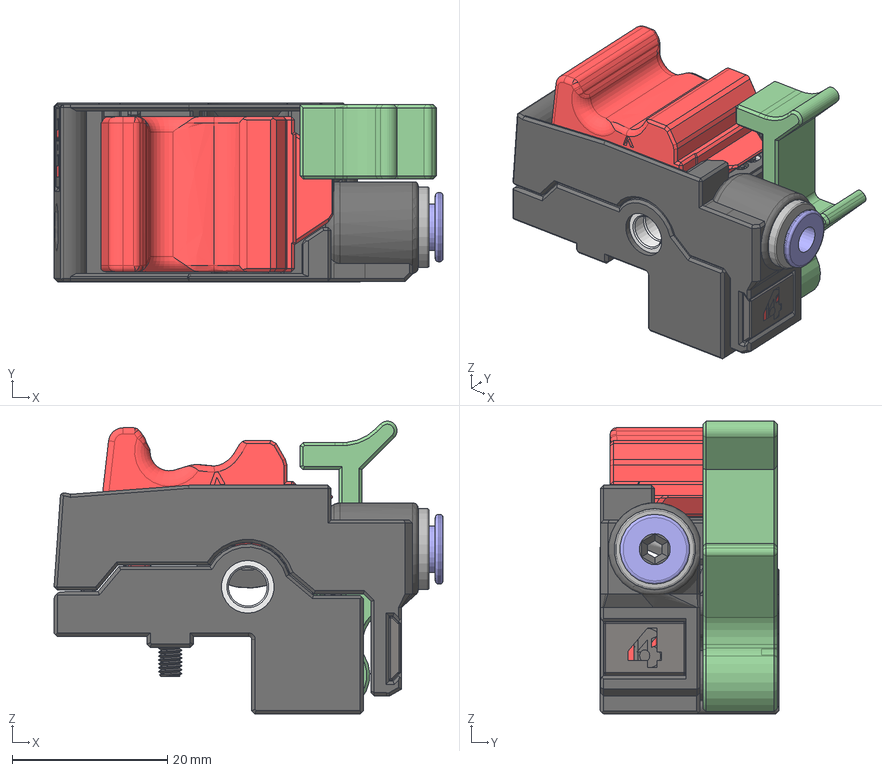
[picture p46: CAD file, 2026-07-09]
CAD/Triple_Decky_C9.step
50.2 x 23.1 x 37.8 mm
Tag plate_0
Tag plate_1
Tag plate_2
Tag plate_3
Tag plate_4
Tag plate_5
Tag plate_6
Tag plate_7
Tag plate_8
Tag plate_9
Tag plate_10
Tag plate_11
Tag plate_12
Tag plate_13
Tag plate_14
Magnet6x3 v1672918 v2
Main body672914
Release clip672915
Seal672916
Tag plate_0 (1) (1)
Tag plate_1 (1) (1)
Tag plate_2 (1) (1)
Tag plate_3 (1) (1)
Tag plate_4 (1) (1)
Tag plate_5 (1) (1)
Tag plate_6 (1) (1)
Tag plate_7 (1) (1)
Tag plate_8 (1) (1)
Tag plate_9 (1) (1)
Tag plate_10 (1) (1)
Tag plate_11 (1) (1)
Tag plate_12 (1) (1)
Tag plate_13 (1) (1)
Tag plate_14 (1) (1)
93245A097_Alloy Steel Flat-Tip Set Screws (2)
99461A917_Phillips Rounded Head Thread-Forming Screws (1)
91290A121_NO THREADS_Alloy Steel Socket Head Screw (1)
stift 3 x 20 (1)^Direct_Drivegear_without_setscrew (1)_Guidler_VORON Clockwork_X Carriage672930 (1) (1)
K3x5x7 Needlebearing (1)^Direct_Drivegear_without_setscrew (1)_Guidle r_VORON Clockwork_X Carriage672932 (1) (1)
Direct_Drivegear_without_setscrew (1)-39^Direct_Drivegear_without_set screw (1)_Guidler_VORON Clockwork_X Carriage672931 (1) (1)
stift 3 x 20 (1)^Direct_Drivegear_without_setscrew (1)_Guidler_VORON Clockwork_X Carriage672930 (1) (1) (1)
K3x5x7 Needlebearing (1)^Direct_Drivegear_without_setscrew (1)_Guidle r_VORON Clockwork_X Carriage672932 (1) (1) (1)
Direct_Drivegear_without_setscrew (1)-39^Direct_Drivegear_without_set screw (1)_Guidler_VORON Clockwork_X Carriage672931 (1) (1) (1)
MR85ZZ v3 v1 (1)
Direct_Drivegear^Driveshaft Assembly_BMG Drive Mechanism_VORON Clockw ork_X Carriage672923 (1)
91290A113_Alloy Steel Socket Head Screw (1)
Magnet6x3 v1672918 v2 (1) (1)

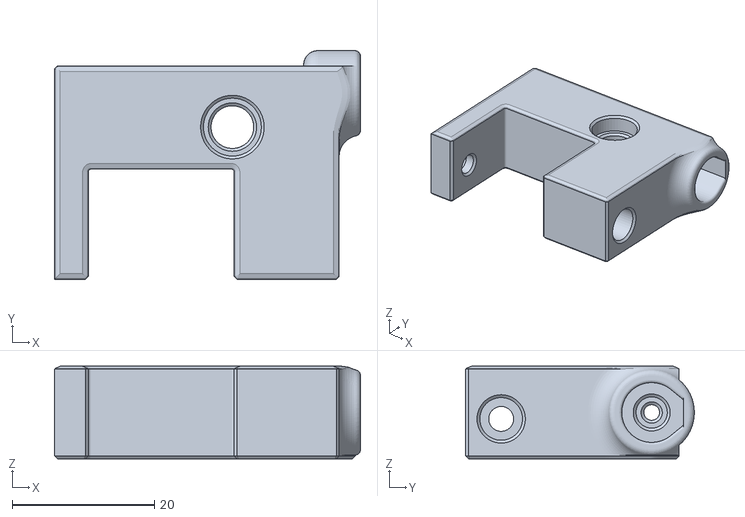
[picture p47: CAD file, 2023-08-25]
STL/ERCF-V2/Bypass_with_ECAS.stl
43.0 x 32.2 x 13.0

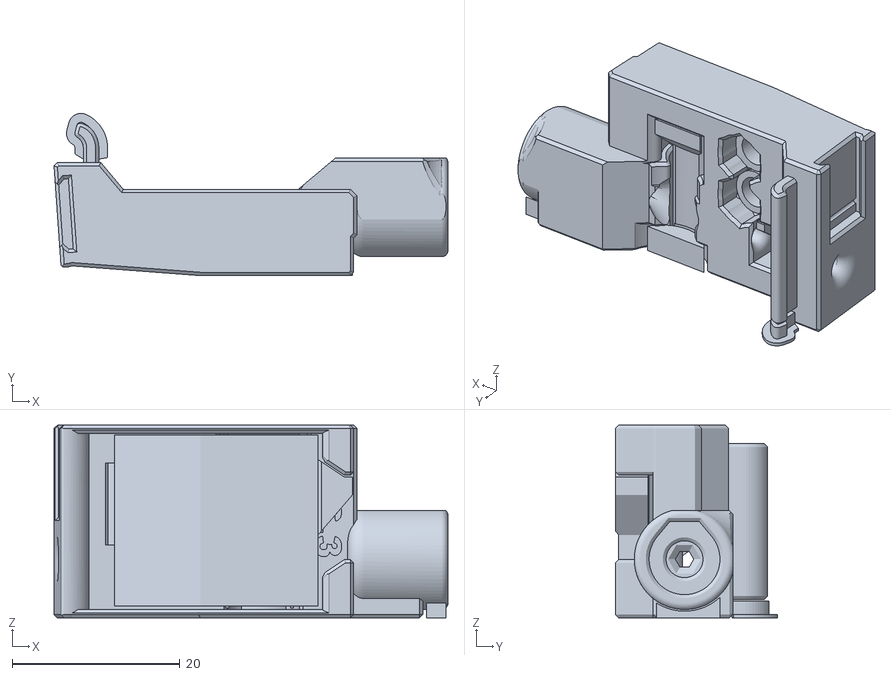
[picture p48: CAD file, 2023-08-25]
STL/ERCF-V2/Rev_C/Rev_C6.3/Filament_Path_for_3_position_Servo/Triple_Decky_Filament_path_3PS_C6_3.stl
47.0 x 19.4 x 23.0

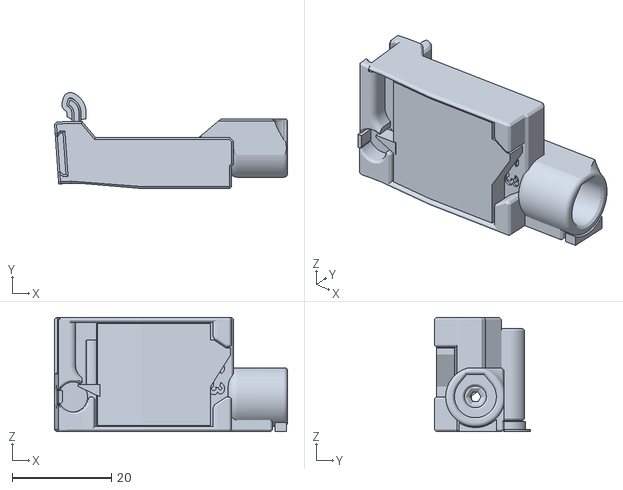
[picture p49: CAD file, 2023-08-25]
STL/ERCF-V2/Rev_C/Rev_C6.3/Filament_Path_With_Magnets/Triple_Decky_Filament_path_For_Magnet_C6_3.stl
47.0 x 19.4 x 23.0

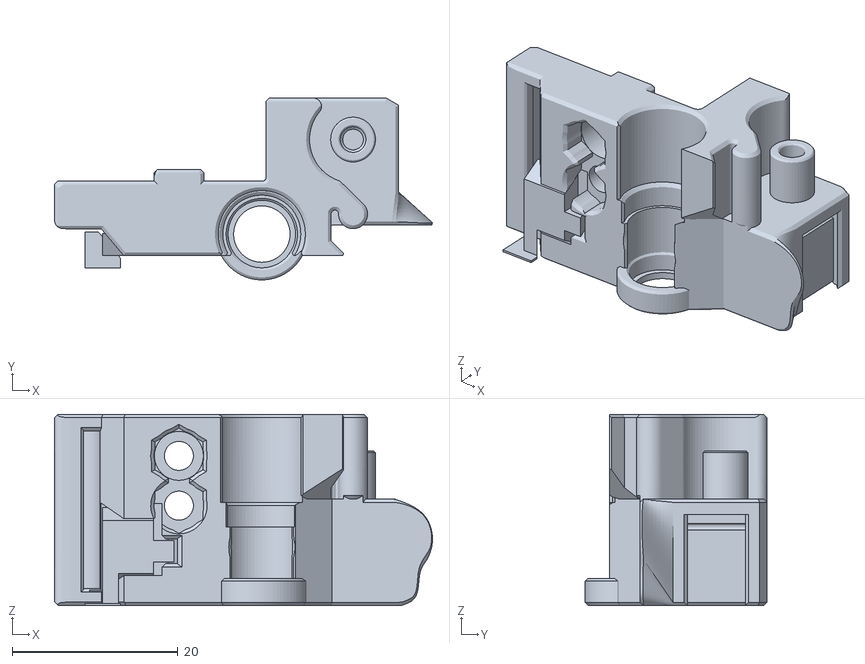
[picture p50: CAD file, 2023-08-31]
STL/ERCF-V2/Rev_C/Rev_C6.3/Triple_Decky_Base_C6_3.stl
45.6 x 21.9 x 23.1

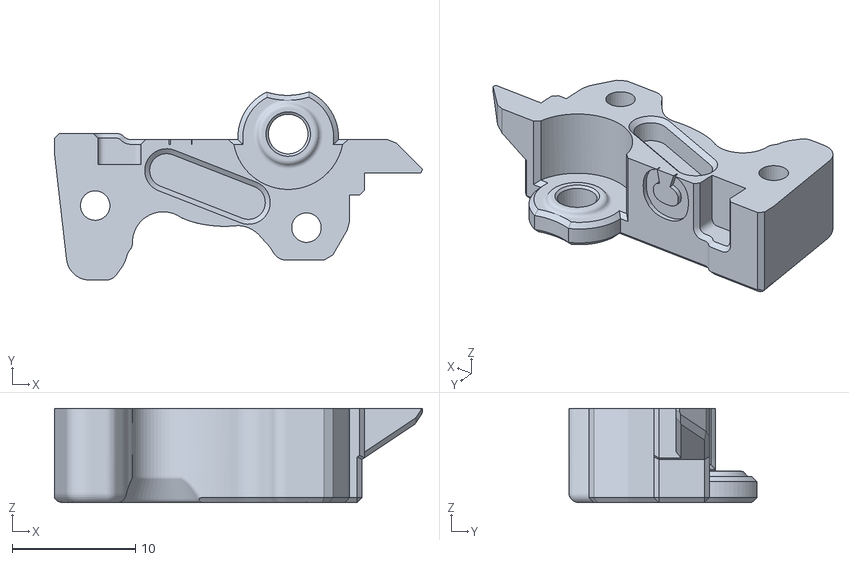
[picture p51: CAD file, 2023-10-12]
STL/ERCF-V2/Rev_C/Rev_C7.0_3PS_only/2 parts tophat option/[a]Triple_Decky_Half_Tophat-integerated_3PS_C70b.stl
29.9 x 15.3 x 7.65

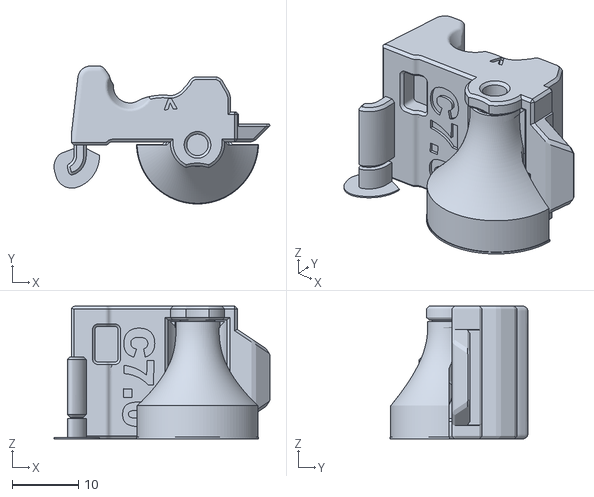
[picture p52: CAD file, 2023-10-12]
STL/ERCF-V2/Rev_C/Rev_C7.0_3PS_only/[a]Triple_Decky_Tophat-integerated_3PS_C7_0.stl
32.5 x 20.8 x 20.0

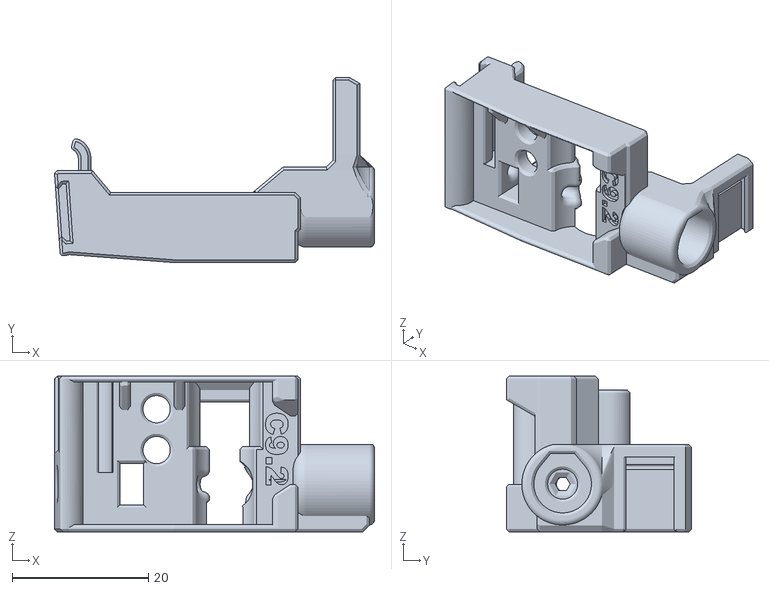
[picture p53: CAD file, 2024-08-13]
STL/ERCF-V2/Rev_C/Rev_C9/Filament_path_C92_xN.stl
47.0 x 27.2 x 22.9

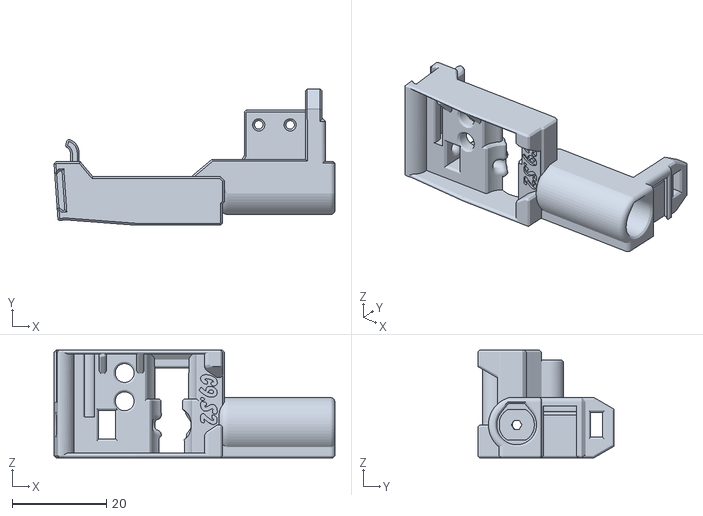
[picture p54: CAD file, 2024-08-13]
STL/ERCF-V2/Rev_C/Rev_C9/Optional Pre-gate Sensor (Experimental)/ECAS/Filament-Path_C9S2_ECAS.stl
59.7 x 29.0 x 22.8

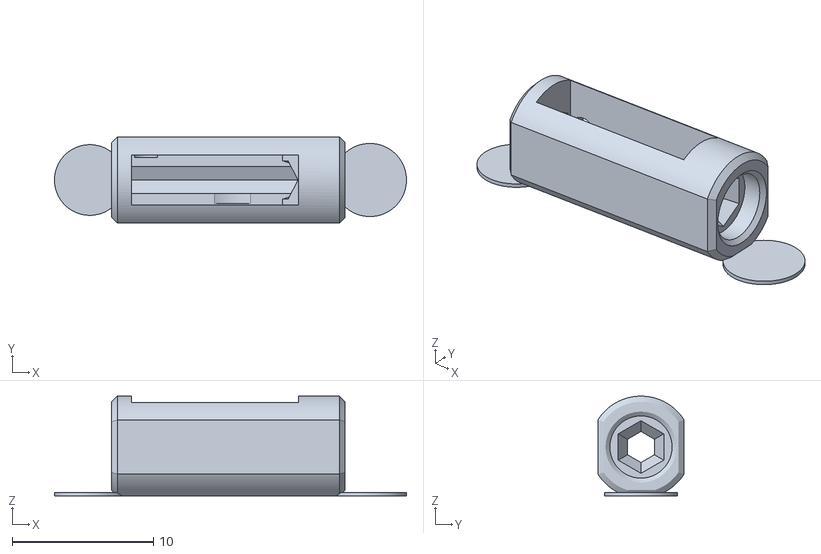
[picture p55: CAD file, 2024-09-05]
STL/ERCF-V2/Rev_C/Rev_C9/Optional Pre-gate Sensor (Experimental)/Insert with brim eyes.stl
24.9 x 6.10 x 7.05

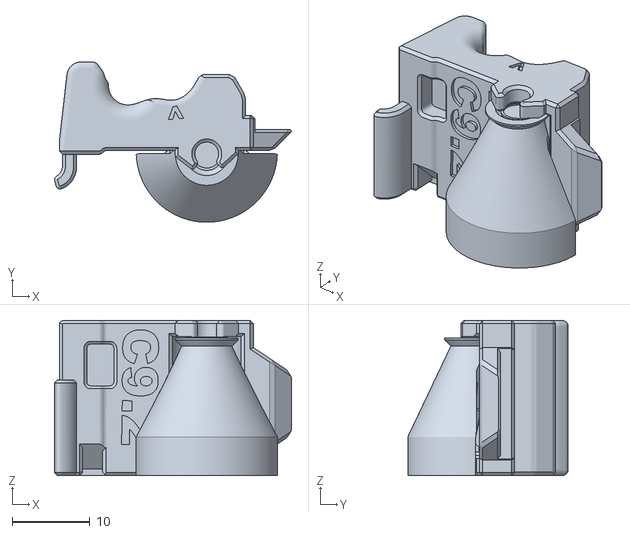
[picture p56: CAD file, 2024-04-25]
STL/ERCF-V2/Rev_C/Rev_C9/Tophat_Option/[a]Tophat-3PS_C92_Low_Profile_Snap_xN.stl
30.5 x 20.7 x 20.0

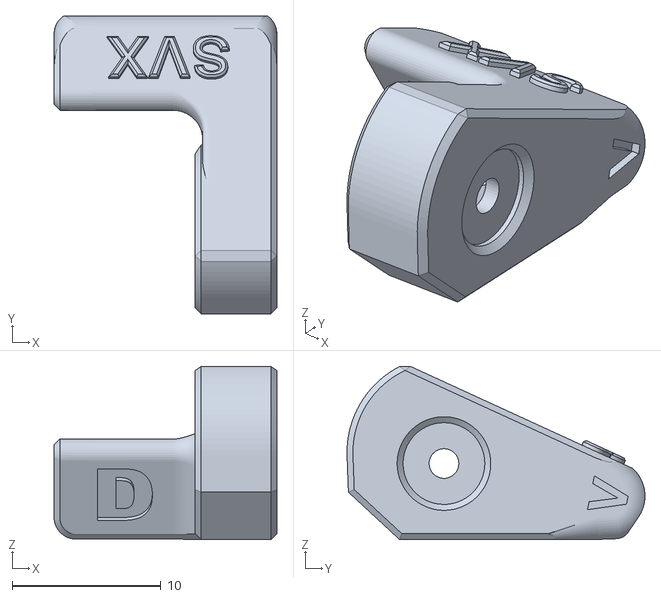
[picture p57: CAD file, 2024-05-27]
STL/ERCF-V2/Rev_C/Servo Arm Savox-3PS-C90Dev-nosupport.stl
15.0 x 20.1 x 11.7

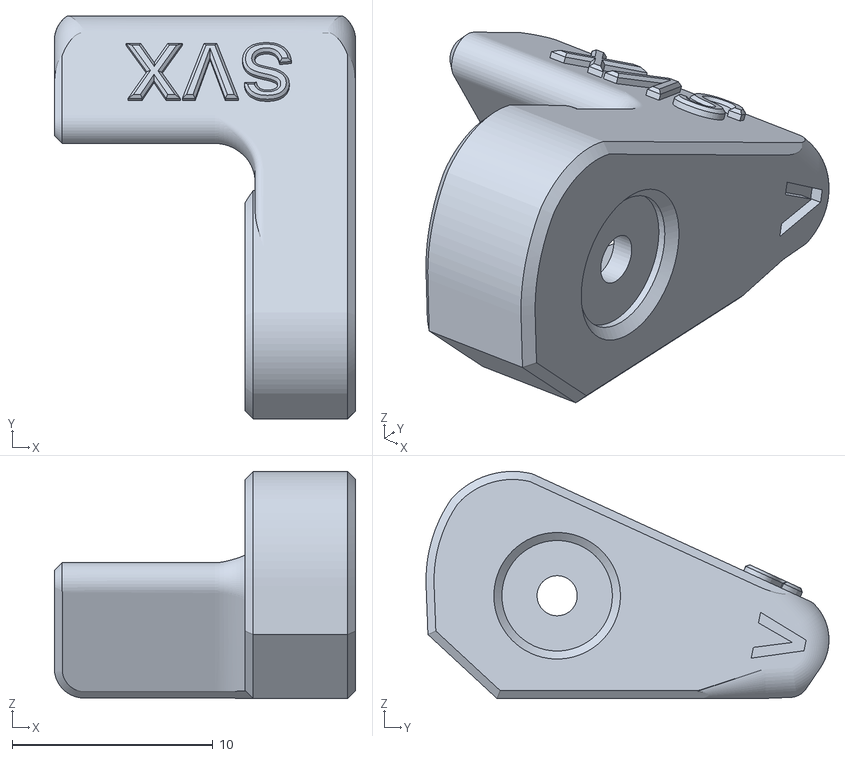
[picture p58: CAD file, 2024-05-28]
STL/ERCF-V2/Rev_C/Servo_arms_for_3PS/Servo_Arm_Savox_C9_Savox_Horn.stl
15.0 x 20.1 x 11.3

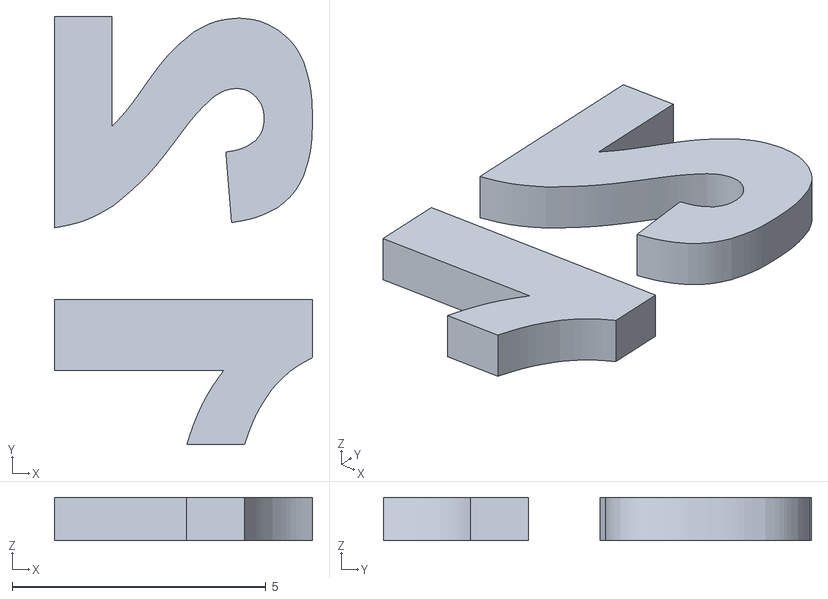
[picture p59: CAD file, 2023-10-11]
STL/ERCF-V2/Rev_C/Tag_plates/Triple_Decky_Tag_plates_Digit12_x2.stl
5.09 x 8.44 x 0.85

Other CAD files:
STL/ERCF-V2/Rev_C/Rev_C7.0_3PS_only/Clearance_options/Triple_Decky_Base_C70_clrearance2.stl
STL/ERCF-V2/Rev_C/Rev_C9/Optional Pre-gate Sensor (Experimental)/Magnet/Filament-Path_C9S2_Magnet.stl
STL/ERCF-V2/Rev_C/Traps/TD_Base_Trap_M3x3_C55.stl
STL/Sturdy Bunny/Rev_B2-B3/[a]Triple_Decky_Tophat-integerated-V_Beta3_3.stl
Archives/Rev_B2-B3/Triple_Decky_Base_Beta3_3.stl
Archives/Rev_B2-B3/Triple_Decky_Filament_Path_Beta3_2.stl
Archives/Rev_B2-B3/Triple_Decky_Filament_Path_Beta3_3.stl
Archives/Rev_B2-B3/[a]Triple_Decky_Tophat-integerated-V_Beta3_3.stl
Archives/Rev_B2-B3/[a]Triple_Decky_Tophat_Beta3_1.stl
Archives/Rev_C/Filament_Path_With_Magnets/TD_Base_Trap_Round_C5.stl
Archives/Rev_C/Filament_Path_With_Magnets/Triple_Decky_Filament_path_For_Magnet_C5_5.stl
Archives/Rev_C/Filament_Path_With_Magnets/[a]Triple_Decky_Tophat-Integrated_For_Magnet_C6_2.stl
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

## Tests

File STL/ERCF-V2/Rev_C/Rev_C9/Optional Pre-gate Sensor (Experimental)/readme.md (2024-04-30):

# C9S : Pre-gate sensor 
## Specifications.
* Since all previous pre-gate sensors uses a 5.5mm ball place in the same vertical plane that the BMG, sometime a notch is ground in the filament from a previous bad load. In this case when the ball drop in that notch, the gate is declared empty by Happy Hare and the print is paused.
* To solve that problem, that best solution would be to orient the ball and the switch in a 90° plane, so the ball can't fall in the notch. This is working very well on specially designed pre-gate sensors, but can't be implemented on the filament path because there are not enough space.
* To solve the problem on the filament path, a special "notch mask" was developed, so the ball never comes in contact with the filament, thus can't fall in the notch and give false triggering.
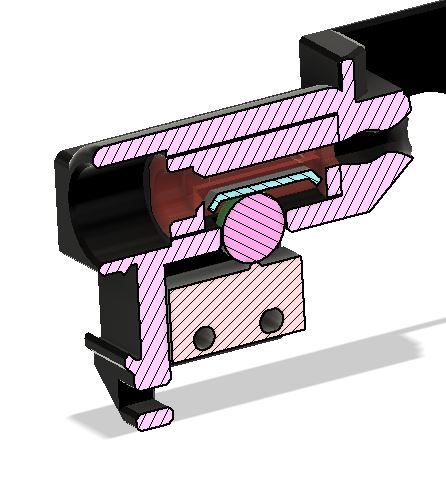
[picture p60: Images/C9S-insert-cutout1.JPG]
  * A flat piece is placed between the filament and the ball to make the notch invisible to the ball. To make that device more stable, the ball is replaced with a 6x3 magnet.
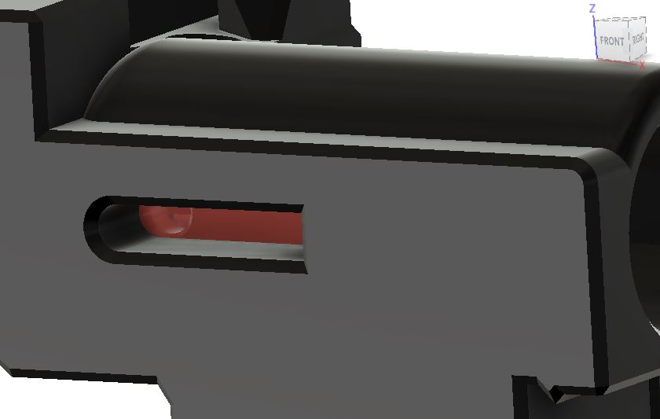
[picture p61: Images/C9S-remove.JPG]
  * For easy installation, an insert is slid together with the interface plate in the filament path. An opening is made on the side of the filament path, so the insert can be removed easily with a 2mm allen key.
  * Since the pre-gate sensor applies a bit of tension on the filament, it is recommended to print the insert and the interface plate in a hard and slippery filament.

 ## How to install and remove it.
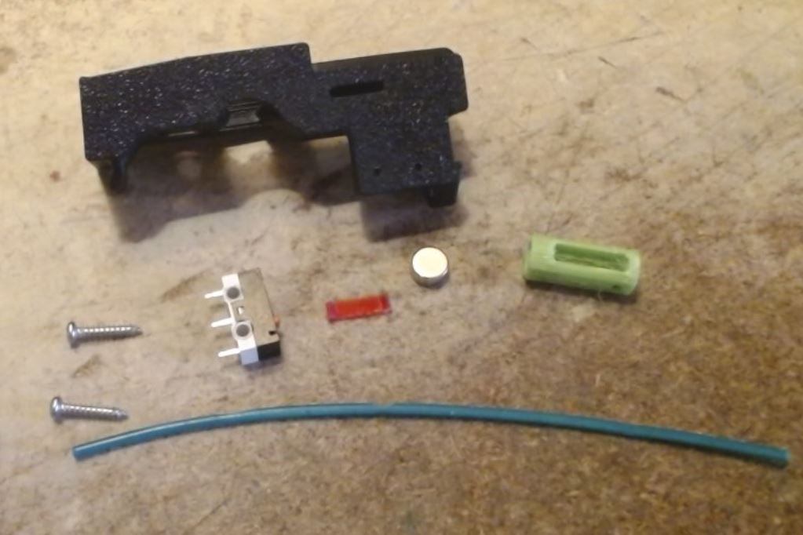
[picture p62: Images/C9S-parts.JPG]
 * **What you need :** 
   * 1 filament path C9Sx
   * 1 insert (green on the picture)
   * 1 interface plate (red on the picture)
   * 1 6x3 magnet
   * 1 Omron switch
   * 2 M2x10 screws
 * **Installation :** 
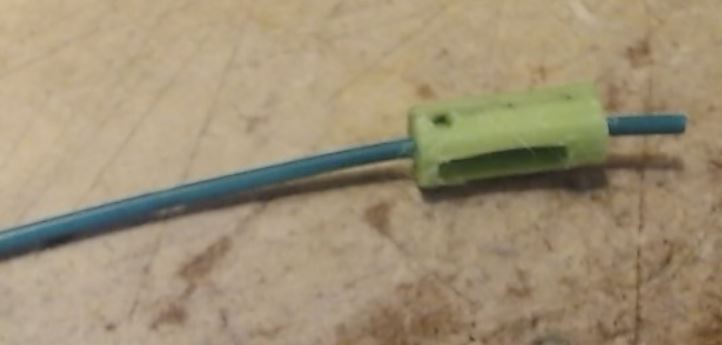
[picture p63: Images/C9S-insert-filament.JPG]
   * Insert a small piece of filament in the insert.
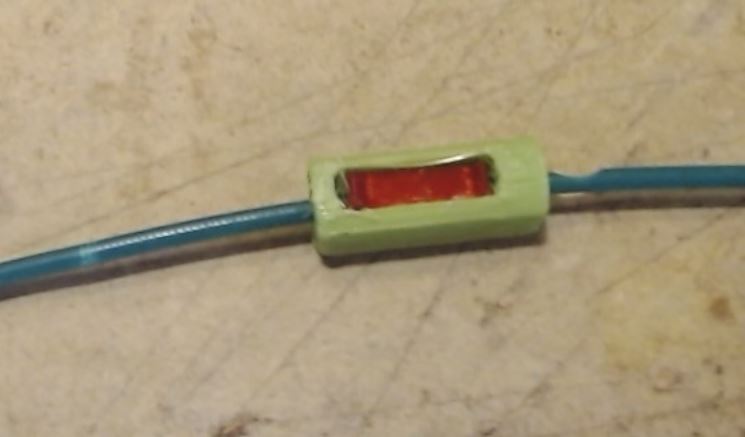
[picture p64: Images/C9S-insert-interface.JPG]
   * Place the insert with the opening up, and drop the interface plate in the opening with the small wings up. The interface plate is provided in 3 different thicknesses (0.7, 0.8 and 0.9mm) for easy adjustment of the behavior of the switch.
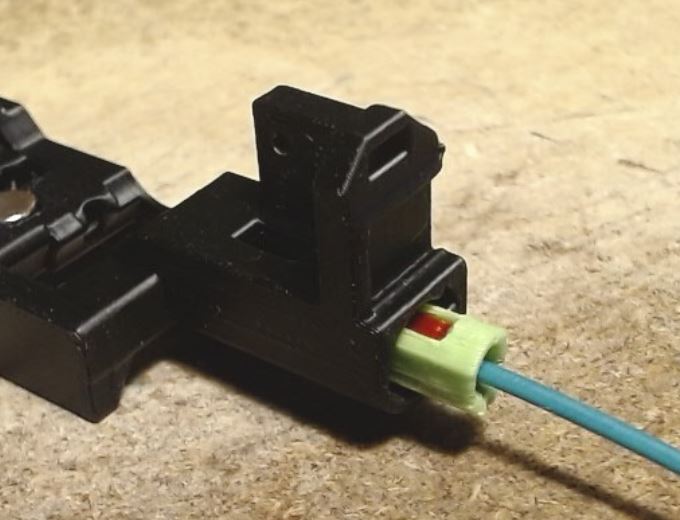
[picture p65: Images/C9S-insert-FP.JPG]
   * Insert the whole assembly in the filament path. The 2mm hole first.
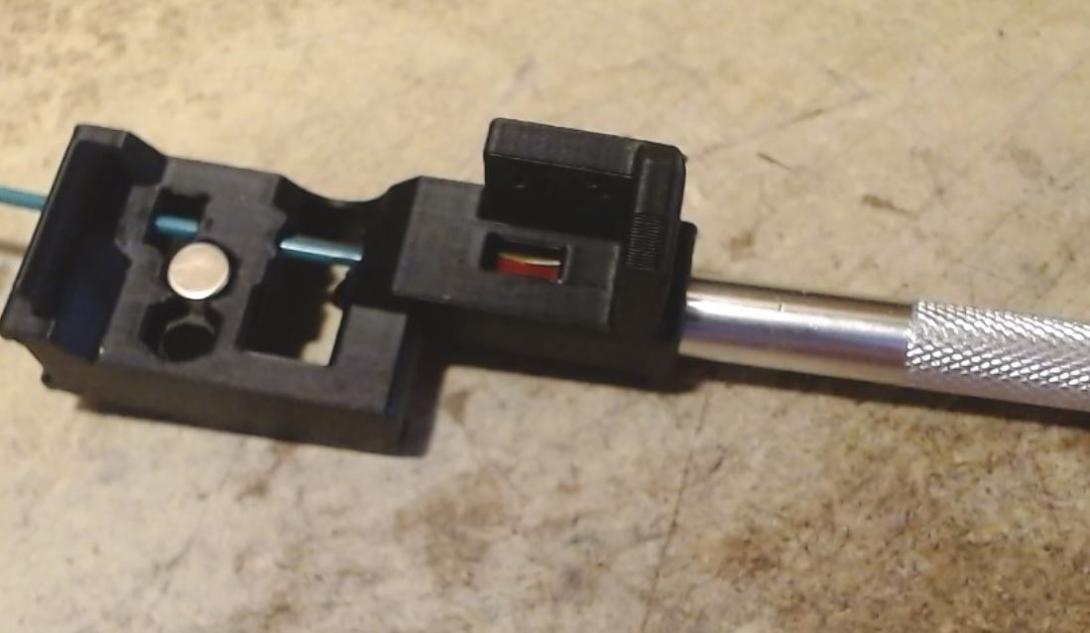
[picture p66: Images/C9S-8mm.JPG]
   * Push the insert fully in with a 8mm rod (x-acto knive, or 8mm drill). Make sure you see the interface plate through the magnet hole.
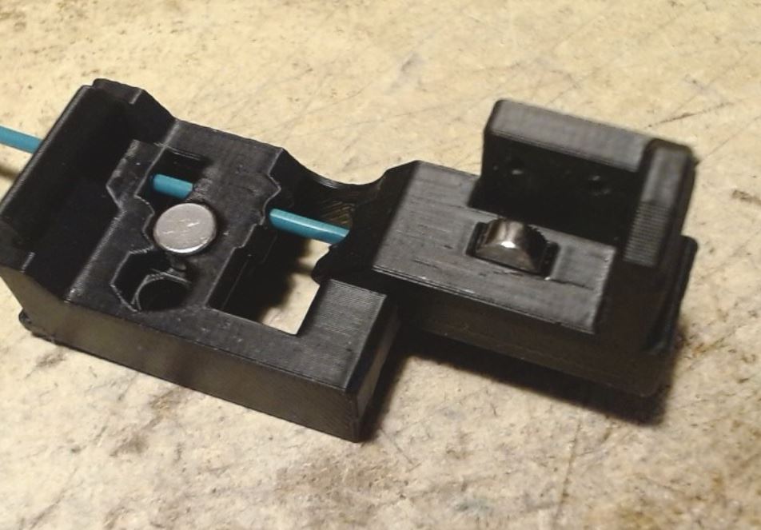
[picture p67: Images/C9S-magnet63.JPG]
   * Place the magnet in the hole.
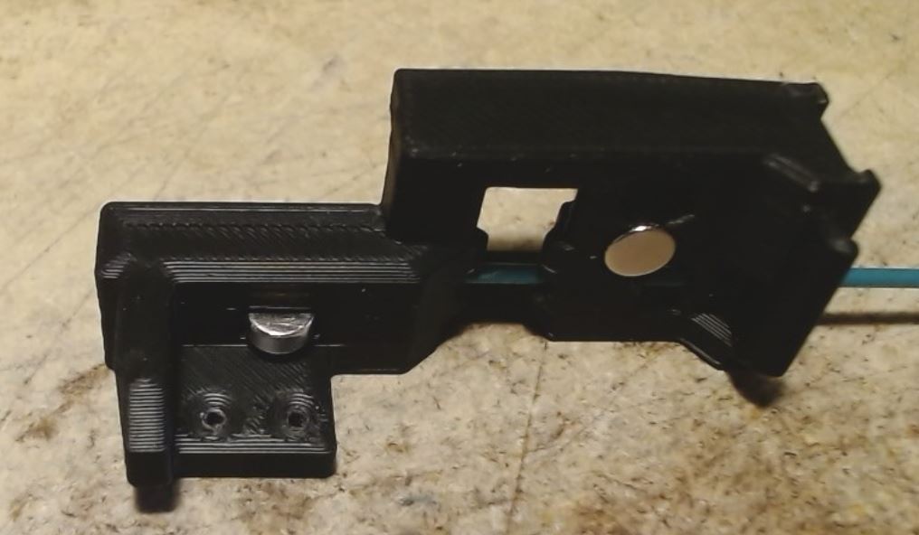
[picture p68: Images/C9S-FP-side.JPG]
   * Keeping the magnet in place with your finger, turn the filament path on its side.
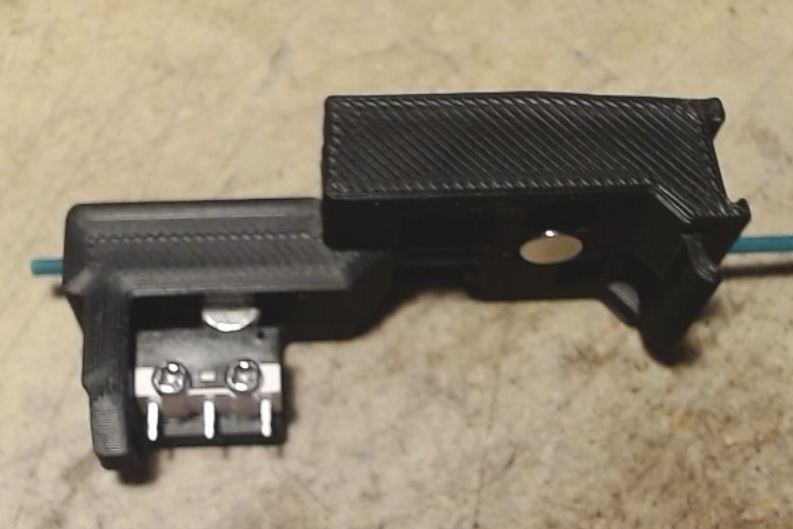
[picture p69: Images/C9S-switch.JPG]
   * Install the switch, and remove the filament. The pre-gate sensor is ready. You can install the filament path on its base.
   * The recommended method to connect the switch the the ERCF board, is to use 90° angled Dupont connectors.
 * **Removing the insert.**
   Since all parts are made from plastic, it is possible that the insert and the interface plate must be replaced at a certain point of time. 
   * Remove the ECAS or magnet entry
   * Remove the switch and the magnet.
   * Turn the filament path on its side so you can see the long 2mm opening.
   * Insert a 2mm allen key on the left side of the opening deeply enough that it goes into the 2mm hole of the insert.
   * Tilt teh allen key to the left, so the insert is pushed out of the filament path. Then put the allen key behind the insert and push it completely out.

## ECAS version.
This is the same as the normal C9.x filament path. The ECAS is simply pushed in. This version will need to extract the ECAS if the insert must be replaced. It is not the preferred version because it is possible that the ECAS does not stay in place after it was removed a few time, and gluing it in place is not a good idea.
## Entry Magnet version.
This is the preferred version, because the entry part is hold in place by a kind of bayonet. It can be removed as often as needed.
The filament path is specially made for that.
* The entry part and ECAS parts need a 10x4mm magnet with a 4mm hole in the center.
  * https://fr.aliexpress.com/item/1005005336565761.html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
* The entry part is inserted in the filament path, and turn 30° CW to lock it in place.
* The counterpart receive the same magnet and an ECAS.
* The magnet assembly is ready.

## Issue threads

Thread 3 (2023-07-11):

Potential modification to ease separation

smwoodward, 2023-07-11:
I printed both the C6_2 and C5_3 of the tophats, mainly to see which one would work better, but something I noticed was I broke one of the end mounts for the BMC gear axel on the first one when clearing the printed supports.  I was able to clear the rest of the supports without problems, but it made me wonder if you were to put a space (similar to the space used between the object and the support to help with removal) between the section of the support that occupies the gear portion of the BMG and the upper part of the support, so that when the support is removed, it breaks in 3 places, top, bottom and middle, this might ease removal of the support along with reducing the risk of breaking the part during removal.

Not sure if it would actually work that way, but just an idea.

gneu42, 2023-07-13:
This is a good idea. I will try that as soon as I'm back home?
Thanks for the idea.

gneu42, 2023-07-14:
I've made this new version, can you test it ?

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

https://www.dropbox.com/scl/fi/nz8lt0ed118amqydt476t/a-Triple_Decky_Tophat-Integrated_For_Magnet_C6_2a.stl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

bakatrouble, 2023-08-07:
Just tried printing this one, and the top section of the three fell out mid-print. I did not have any trouble removing the simgle-piece support of the 3P servo version.

gneu42, 2023-08-07:
The previous version is still available in the archive folder.
   [a]Triple_Decky_Tophat-Integrated_For_Magnet_C6_2.stl
Only the support is different.

bakatrouble, 2023-08-07:
I went another way, reinforced this separated support with a cylinder primitive in slicer

gneu42, 2023-09-04:
Stl is changed.

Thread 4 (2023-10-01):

Clearance...

Durahl, 2023-10-01:
With one of the ECAS04 Fittings having come loose on my Stock ERCF I decided to give the whole thing an overhaul including the SturdyBunny, Springy, and... well... TrippleDecky 😑

While the first two worked without issues I cannot say the same for the TrippleDecky which I mostly attribute to the use of _terrible_ if at all use of clearances and lack of documentation of how the system should behave _in operation_ ( like a Video showcasing if parts should fit loose or in tension together?! ).

**First, the _very_ Obvious:**
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
Both the stationary `Base` as well as the `Filament Path` have the same height on the Build Plate thus resulting in the same width on the Extrusion.

Everyone _packing_ the `Bases` together as tight as possible to honor the concept of a **Sturdy**Bunny will essentially _also_ pack the `Filament Paths` together resulting in them binding against each other.
Everyone leaving a gap between the Bases via the use of like a paper shim during assembly will defeat the concept of a SturdyBunny.

The _obvious_ choice is to increase the Z-Height of the `Base` on the Build Plate by at least 1 if not 2 Layers.

**Next, the Questionable:**
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
Even with the above-mentioned Hack I couldn't get the `Filament Path` parts to move _reliably_ free despite the use of 4 Magnets like how it is happening with regular `Blocks` and the `Top Hats` on the Stock / SturdyBunny Variants. And the parts print to spec because the `MR85ZZ Bearings` do fit nicely!

This I attribute in parts to how the `Trap` is getting caught in the square hole of the `Filament Path` it is supposed to reside in but also how there's essentially NO clearance whatsoever between the Hinge Areas of the `Base` and `Filament Path` as can be seen above.

**Finally, the Unknown:**
Is the `Integrated Top Hat` supposed to be floppy like on a Stock / SturdyBunny or is it supposed to be press fit tight with the `Filament Path`? Who knows... Mine wouldn't move on their own once attached to the Filament Paths and while them not moving freely wouldn't make much of a difference in the grand scheme of things it then kinda begs the question why they're a separate part from the `Filament Path` to begin with?

**Verdict:**
Didn't work out for me... At the end of the day the amount of pressure required to overcome the tension in the System for the Filament to even just remotely reliably getting fed through the Tube would have exceeded the strength of a SAVOX SH-0254 getting past the Springys spring tension.

So SturdyBunny / Springy which is working like a charm ( after splicing my own _working_ `Integrated Top Hat` together ) it is for me.

gneu42, 2023-10-03:
I'm sorry that TD did not work for you.

Triple Decky was designed to solve only 1 problem. That is the filament going out of the block either forward or backward when loading/unloading other tools. If you do not have that problem, then you don't need it. You can go with the original design from Sturdy Bunny, and keep the magnetic gates.

The very obvious : looking at your pictures, you are not printing it the way you should. If you print all the parts separately, and if YOUR PRINTER IS WELL TUNED, and you use the correct profile (e.g. from Andrew Ellis like it is mentioned in the readme file). The hinged parts should go together without any force nor clean up, beside  very little cleaning where the support was located and what is described in the cleaning tips on the readme file. Lots of people have print TD without issues.
Also, 3D printers are not precisions machines like a mill or a lath. It is impossible to make STL for each printers. A lots of variables can affect the way parts fit together, filament type/brand, temperature... If with your set up, you can't get them to fit nicely, then you can always file / sand the area that are causing problems. With all the feedback I get, it seems that it works very well for lots of people.

Bunny is sturdy because of the 2020 extrusion, not with packing the gates together as hard as possible. It is not necessary to pack all the block together like on V1. Just put all the blocks next to each other and all will be fine. However I agree that both parts have the same width, and I'm looking to make a small change in that respect. Unfortunately, I can't do it right now. I not at home at the moment, and can't test.

Concerning clearance, I will not change anything because it works just fine the way it is for the vast majority of people who have printed them.
However, if you wait for the V2 public release, you will have access to the CAD file and then you can modify whatever you like.

The top hat should be freely moving on its hinge and not floppy like on V1.

I will also try to make a small video showing how parts are fitting together. This might take some time because I may not have everything handy where I am right now.

I will make a small modification just for you to try concerning the width of the filament path (it will be reduced by 1 layer) and send it to you via discord DM.

Durahl, 2023-10-04:
I think it goes without saying that I did _NOT_ print the `Base` and `Filament Path` in a print in place assembled state.
Them being pictured like that in the Slicer was to show the lack of clearance between the two parts from even just a Slicer PoV.

My Printer is tuned well enough hence my comment about the MR85ZZ Bearings fitting nicely in their Bearing Pockets.
If they were loose or hard to press in, they'd be an indicator of something being off but that is not the case.

3D Printers not being CNC Precision Machines capable of holding 1/100th of a Millimeter Tolerances is the _very_ reason why such Projects should be designed with loser Tolerances in mind which clearly isn't the case. Just saying "It works for some" is no basis for sticking with it. Might as well close this Bug Report section altogether! Neither is telling ppl to whip out a File / Sanding Paper and go ham on the parts until they fit - Especially since for anyone with this issue it won't even be clear where the problem is.

If you're asking for such tight tolerances nearing that of a CNC then it is your job as the Author to either account for variances in Printers, Materials, and Slicers **_OR_** providing the _exact_ settings for the Machine, Slicer, and Material you can guarantee your Project will work with. Everything else is just wasting ppls Time and Materials - Especially those willing to giving it a try and contributing to making it better.

But you've made your point it is not worth further investigating the TrippleDecky since you're not even willing in making such a miniscule change like adding a mere 1-2 additional Layers to the `Base` to aid against the friction between the `Filament Path` as such I will stop providing suggestions based on my experience in making it an _universally_ reliable product for _everyone_ instead of just the lucky few that won the Machine, Slicer, and Material Lottery.

Closed 2023-10-04.

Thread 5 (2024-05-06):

C9 Magnet issues ECAS-magnet STL and FB-Magnet STl too small for standard 10mm magnets

Urminme, 2024-05-06:
Ive tried printing these several times but the holes on the STL measure around 9.5mm and the magnets are 10mm exactly so they just dont fit and if forced break the plastic, Ive tried printing with less walls but even then its just too small, Do you have a newer file that is the correct one or specific settings for these pieces

gneu42, 2024-05-07:
Yes, your are right. I made them so my magnets fits.
My 10mm magnet are 9.5mm OD. I suppose that depending of the magnet manufacturer, it will change a bit.
I will make new part for 10mm.

gneu42, 2024-05-07:
New files are uploaded?
Was tested with 10mm drill bit, because my magnets are 9.6mm OD

Urminme, 2024-05-12:
Thank you very much for the update that fits perfectly!

gneu42, 2024-05-13:
Your welcome.

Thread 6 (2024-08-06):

C9 Magnetic ECAS, Can we spare the magnets?

iwm911, 2024-08-06:
while waiting for my magnets to deliver for the new c9 pregate sensors experimental filament path i was thinking, why not combine the lockable magnet entry part with the ecas part?
i meshed them together printed them out for a test.

it looks pretty good, allows easy maintenance and accessibility and does not require magnets (or anything more then the original design).

Then why not?

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

gneu42, 2024-08-07:
Yes, that's a good idea.

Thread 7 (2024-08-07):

Can you publish CAD files for easy modification?

lk8716047, 2024-08-07:
May I ask if it is possible to add a C9 version with three layers of locks? I have encountered a problem with the current version and don't know which one to use correctly. Or publish CAD files for easy modification, thank you!

gneu42, 2024-08-07:
What do you mean by "three layer of locks" ?
What problem did you have ?

iwm911, 2024-08-08:
i dont have a problem with the layers of lock (whatever that is) but i will be happy to get a CAD for modifications.
i have some ideas that might benefit with Triple Decky and some free time to create pull requests.

right now i am working on the STLs but that's not fun at all.

gneu42, 2024-08-09:
I understand your concern, but I will upload the CAD when ERCF RC2 will be released.

lk8716047, 2024-08-09:
Thank you very much！

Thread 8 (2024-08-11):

Filament Sensor reconsideration

iwm911, 2024-08-11:
Hi,

i think it's might be worth a while to reconsider the filament sensor component in the new triple decky with sensors.

i think that the proposed solution of 2 printed parts with the magnet could be a bit over engineering.

i had great success with the  cotton tale sensors (with the bearing ball and the micro switch) by adding a printed spacer between the ball and the micro switch.

i have printed one for each gate and had 100% accurate results.

This the model i created is as follows:
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

gneu42, 2024-08-12:
I had bad experiences with CT sensor style. Lots of false triggering.
On future versions, the magnet could be replaced by something else, but not a ball.

iwm911, 2024-08-12:
maybe something like the Prusa filament sensors?
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

i just think that the current solution with the printed parts the wear will be noticeable very quick

gneu42, 2024-08-12:
If there is a notch in the filament. The sensor should not see it.
That is the main problem of all the sensors that are below the filament. They are just unusable, unless you disable all the sensors when you print. But then you can't use end of spool.
On this one I don't know in which plane the sensor is.

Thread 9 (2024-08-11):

JST PH2.0 Connectors for filament sensors

iwm911, 2024-08-11:
It's still a work in progress but i thought about making the filament sensor as a complete unit with JST PH2.0 connector.

i modeled something but it's in the very early stage.
the idea is to have the filament switch and the JST connector coupled together on a cover plate and when closed the whole switch and jst are fixed in place.
the connector it from the bottom to allow the springiness of the wires to "help" the magnet and prevent it from sinking.

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

gneu42, 2024-08-12:
The idea is not bad, but I think you will have interferences with the latch.
My experience has proven that sometime you need to be abel to diconnect the switch easily. So for me XT connector are not ok. They will be difficult to remove. Especially under the filament path. I will stay with Dupont.

iwm911, 2024-08-12:
the whole idea of the JST PH2.0 connectors is that they are easily detachable, but does provide some locking mechanism so they wont fall off like a Dupont may.

Dupont are great for prototyping and breadboards but i think that in "production" it will be better to have something more standard which will make sure the cable stays connected.

gneu42, 2024-08-12:
I never had dupont disconnecting themselves.
You will not have enough access to disconnect the JST. at least on my setup.

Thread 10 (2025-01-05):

Pre-Gate sensor option for C9 that uses lever switches?

piotrb, 2025-01-05:
Just looking at my pre-gate sensor options and I feel torn between a few things ..

I tried working with the Experimental C9 pre-gates, and they seem quite finicky .. not my jam anyways :)

There is this mod for C7 here: https://github.com/juliusjj25/ERCF-Pregate-Sensors

This uses D2F-L3-D3 switches which seem like so much of a simpler option :)

Heck, someone even made a standalone version of this which you can plug inline (I don't really love that either, I do like the pre-gates being very close to the gears myself) -- https://github.com/igiannakas/Standalone-lever-switch-pre-gate-sensor-for-ERCF-v2

I'm probably going to end up printing off a few of these C7 based ones and testing them (I already ordered the switches), but I do like a bunch of the improvements in C9, so I would love to be able to have it work with that instead .. just saying :)

gneu42, 2025-01-06:
I know that C9 with pre-gate sensor is a bit complicated, but all the other type with the ball or lever under the possible notch in the filament caused by grinding are prone to false triggering. C9 tries to avoid false triggering.

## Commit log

2023-05-31 Add Gate plate multicolor
    [Magnetic gate_00.stl, Magnetic gate_01.stl, Magnetic gate_02.stl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]
2023-05-31 Rename Tophat integrated
    [[a]Triple_Decky_Tophat-integerated-V_Beta3_3.stl]
2023-06-01 Re-upload filament path 3.2
    [Triple_Decky_Filament_Path_Beta3_2.stl]
2023-06-07 Add version B4
    [Tag_Gate_0.stl, Tag_Gate_1.stl, Tag_Gate_10.stl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]
2023-06-07 Removed old tag plates
    [Magnetic gate_00.stl, Magnetic gate_01.stl, Magnetic gate_02.stl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]
2023-06-08 Add Rev C5
    [TD_Base_Trap_C5_Round.stl, TD_Base_Trap_C5_Screw.stl, TD_Base_Trap_C5_V-Shape.stl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]
2023-06-08 Add C5-magnet
    [Tophat-integerated_Universal_C5_3.stl, Triple_Decky_Filament_Path_3_Pos_Servo_C5_3.stl, Triple_Decky_Filament_Path_With_Magnet_C5_3.stl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]
2023-06-09 Add C5.4 with magnet in the middle
    [Filament_path_with_magnet_C5_4.stl, Triple_Decky_Base_C5_4 .stl]
2023-06-11 update Tag : digits are 0.4mm inside
    [Tag_Gate_0.stl, Tag_Gate_1.stl, Tag_Gate_10.stl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]
2023-06-11 Update tag with digits 0.4mm inside
    [Tag_Gate_0.stl, Tag_Gate_1.stl, Tag_Gate_10.stl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]
2023-06-14 Update C5
    [Filament_path_with_magnet_C5_4.stl, TD_Base_Trap_C5_Screw.stl, TD_Base_Trap_C5_V-Shape.stl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]
2023-06-15 Update Rev C
    [TD_Base_Trap_C5_Screw.stl, TD_Base_Trap_C5_V-Shape.stl, TD_Base_Trap_M3x3_C55.stl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]
2023-06-17 Update STLs
    [TD_Base_Trap_C5_Screw.stl, TD_Base_Trap_C5_V-Shape.stl, TD_Base_Trap_M3x3_C55.stl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]
2023-06-27 Update RevC with C6_x
    [TD_Base_Trap_M3x3_C55.stl, TD_Base_Trap_Round_C5.stl, TD_Base_Trap_V-Shape_C56.stl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]
2023-06-28 Correct print orientation
    [Triple_Decky_Filament_Path_For_Magnet_C6_2.stl, Triple_Decky_Filament_path_For_Magnet_C5_5.stl, [a]Triple_Decky_Tophat-Integrated_For_Magnet_C6_2.stl]
2023-07-09 Update [a]Triple_Decky_Tophat-Integrated_For_Magnet_C6_2.stl
    Clearance hole for the trap was too small.
    [[a]Triple_Decky_Tophat-Integrated_For_Magnet_C6_2.stl]
2023-07-20 Reorganize STL's and add Rev C for 3 position servo
    [Servo Arm MG90S_for_3PS.stl, TD_Base_Trap_M3x3_C55.stl, TD_Base_Trap_Round_C5.stl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]
2023-07-21 Update readme files for Rev C 3PS
    [[a]Triple_Decky_Tophat-integerated_Universal_Mag&3PS_C6_0.stl, [a]Triple_Decky_Tophat-integerated_Universal_Mag&3PS_C6_1.stl]
2023-07-21 Update readme and images for Rev C
    [[a]Triple_Decky_Latch_Beta3_1.stl, [a]Triple_Decky_Latch_RevC6_0.stl]
2023-07-23 Update read me with assembling tips
2023-07-23 Update readme and correct tophat names
    [[a]Triple_Decky_Tophat-integrated_3PS_C6_2.stl, [a]Triple_Decky_Tophat-integrated_Universal_Mag&3PS_C6_0.stl]
2023-07-23 Create Servo Arm Savox.stl
    [Servo Arm Savox.stl]
2023-07-23 Create savox servo arm
    [Servo_Arm_MG90S_for_3PS.stl, Servo_Arm_Savox_for_3PS.stl]
2023-07-28 New tophat with shorter tang.
    Starting tophat C6.3, to avoid clearance problem with some ABS material, the tang is shorter by 0.2mm.
    All previous version can be filed down if it does not move freely in the filament path.
    [[a]Triple_Decky_Tophat-Integrated_For_Magnet_C6_3.stl, [a]Triple_Decky_Tophat-integrated_3PS_C6_3.stl, [a]Triple_Decky_Tophat-integrated_Universal_Mag&3PS_C6_3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]
2023-07-28 Remove previous versions of tophats
    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
    [[a]Triple_Decky_Tophat-Integrated_For_Magnet_C6_2.stl, [a]Triple_Decky_Tophat-integrated_3PS_C6_2.stl, [a]Triple_Decky_Tophat-integrated_Universal_Mag&3PS_C6_0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]
2023-08-25 Add new updated STL and update readme
    [Bypass_with_ECAS.stl, Servo_Arm_MG90S_for_3PS.stl, Servo_Arm_Savox_for_3PS.stl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]
2023-08-25 restore SB name + update readme
    [Bypass_with_ECAS.stl, Servo_Arm_MG90S_for_3PS.stl, Servo_Arm_Savox_for_3PS.stl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]
2023-08-28 Archive old versions
    [Triple_Decky_Filament_Path_For_Magnet_C6_2.stl, Triple_Decky_Filament_path_3PS_C6_1.stl, Triple_Decky_Filament_path_RevB4_1.stl]
2023-08-30 Update readme with servo arm.
2023-08-31 Add Base C6.3
    [Triple_Decky_Base_C6_3.stl]
2023-09-01 Move Base C6.0 to archive
    [Triple_Decky_Base_C6_0.stl]
2023-09-07 Update the latch screw size
2023-10-03 Update readme with short assembling video.
2023-10-11 Add C7.0 Stls + images
    [Triple_Decky_Base_C70_clrearance1.stl, Triple_Decky_Base_C70_clrearance2.stl, Triple_Decky_Base_C7_0.stl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]
2023-10-12 Update STL, images, readme.
    [Triple_Decky_Base_C6_3.stl, Triple_Decky_Base_C70_clrearance1.stl, Triple_Decky_Base_C70_clrearance2.stl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]
2023-10-12 Correct tophat C7.0
    [[a]Triple_Decky_Half_Tophat-integerated_3PS_C70a.stl, [a]Triple_Decky_Half_Tophat-integerated_3PS_C70b.stl, [a]Triple_Decky_Tophat-integerated_3PS_C7_0.stl]
2024-04-25 Add C9 and C9S STLs
    [Filament path C90_xN.stl, Filament_path_3PS_C9S1.stl, Insert.stl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]
2024-04-28 Update C9
    [ECAS_Magnet.stl, FB-Magnet_Entry.stl, Filament-Path_C9S1_Magnet.stl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]
2024-04-29 Add thicker interface plates
    [Interface_plate_0.7_PETG.stl, Interface_plate_0.8_PETG.stl, Interface_plate_0.9_PETG.stl]
2024-04-30 Update interface plates
    [Insert with brim eyes.stl, Interface_plate_0.7mm.stl, Interface_plate_0.8mm.stl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]
2024-05-01 Update filament path for pre-gate sensor - made the Dupont hole bigger
    [Filament-Path_C9S1_ECAS.stl, Filament-Path_C9S1_Magnet.stl, Filament_path_3PS_C9S1_ECAS.stl]
2024-05-07 Add Magnet holder for 10mm magnets. Originals were 9.6mm
    [ECAS_10mm_Magnet.stl, ECAS_9.6mm_Magnet.stl, FB_10mm_Magnet_Entry.stl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]
2024-05-27 Create Servo Arm Savox-3PS-C90Dev-nosupport.stl
    [Servo Arm Savox-3PS-C90Dev-nosupport.stl]
2024-05-27 Add servo arm images
2024-05-28 Update readme with savox servo horn version of servo arm.
2024-06-07 Update readme for C9 pre-gate
    [ECAS_10mm_Magnet.stl, ECAS_9.6mm_Magnet.stl, FB_10mm_Magnet_Entry.stl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]
2024-07-10 Rename Sturdy bunny -> ERCF-V2
    [Bypass_with_ECAS.stl, ECAS_10mm_Magnet.stl, ECAS_9.6mm_Magnet.stl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]
2024-08-13 Update TD C9 : fix for M2x10 SHCS
    [Filament path C90_xN.stl, Filament_path_C92_xN.stl, Triple_Decky_Base_C91_xN.stl]
2024-08-13 Update C9 pre-gate with correction for M2x10 SHCS
    [Filament-Path_C9S1_ECAS.stl, Filament-Path_C9S1_Magnet.stl, Filament-Path_C9S2_ECAS.stl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]
2024-09-05 Update Insert with brim eyes.stl
    This mod should avoid the filament to be catched when the natural curve of the filament is pointing down.
    [Insert with brim eyes.stl]
2024-09-05 Update Insert with brim eyes.stl
    [Insert with brim eyes.stl]
